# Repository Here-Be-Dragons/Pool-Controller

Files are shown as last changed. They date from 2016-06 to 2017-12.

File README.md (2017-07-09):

# Automated Pool Controller
###### Timer Control of a Hayward Tristar VS Pump and Hayward GL-235 Solar Pool Controller
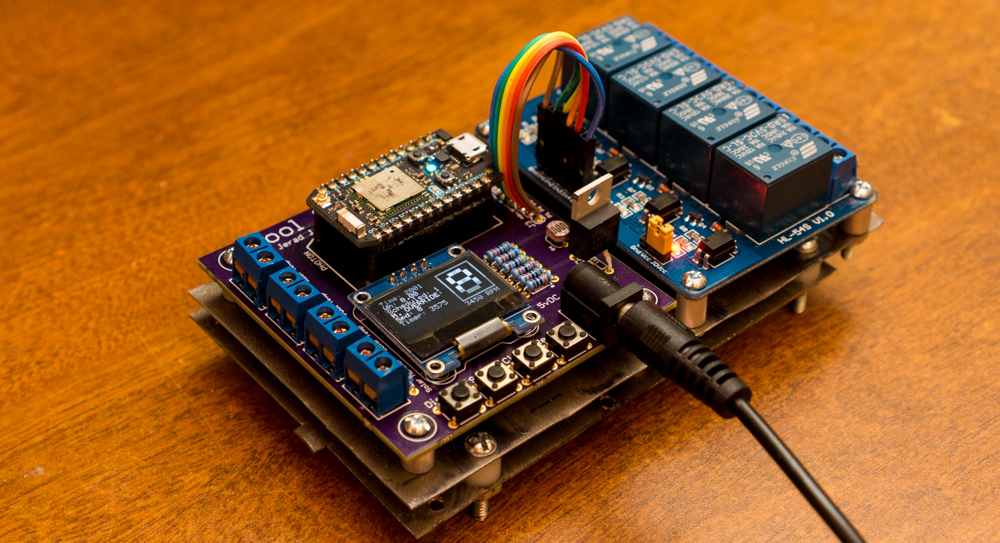
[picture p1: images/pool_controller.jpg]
Finished Pool Controller
  
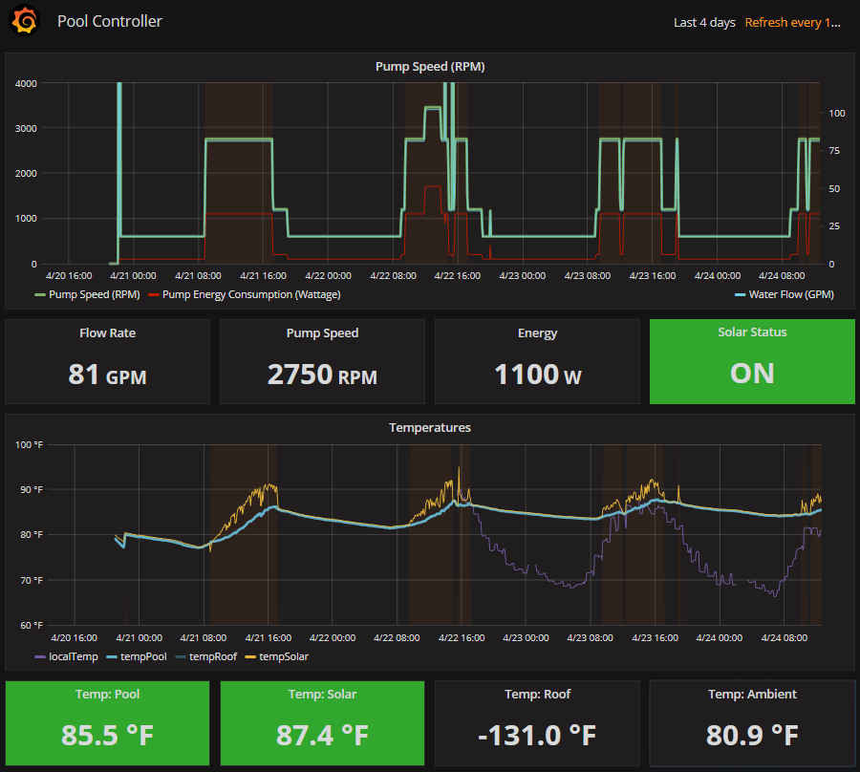
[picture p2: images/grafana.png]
Grafana Dashboard

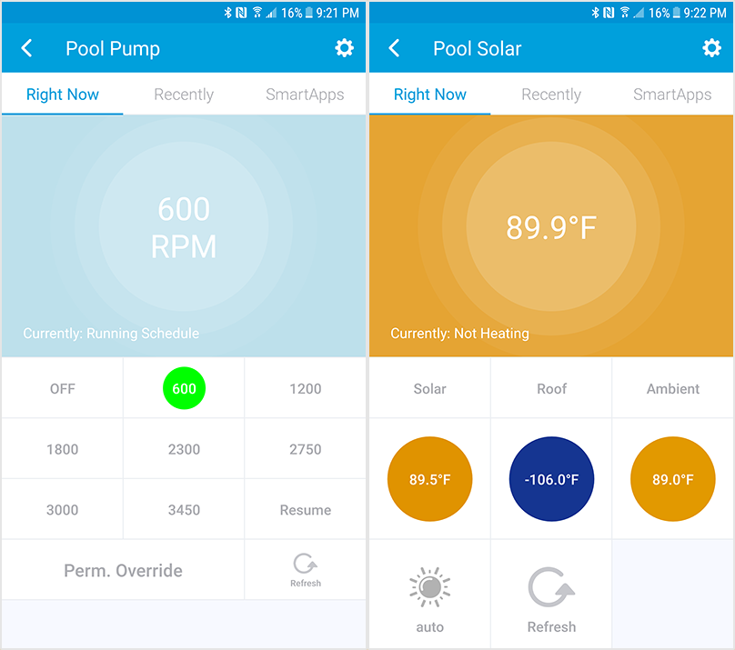
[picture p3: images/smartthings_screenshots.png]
SmartThings Integration

### Overview
---------------------
**Background:**
Due to the engineering principle known as the Pump Affinity Law (<https://en.wikipedia.org/wiki/Affinity_laws>), a very significant energy savings can be had by reducing the speed at which you run your pool pump (approaching 90% savings in an optimal configuration vs. a single-speed pump).  The ideal configuration for energy savings would be to run a pump 24-hours a day at the lowest setting possible to still achieve desired water pumping volume (rule of thumb: 1 pool's water turnover per day), with needed speed-ups at various points during your day to enable the skimmer/vacuum/etc to function.  

My solar heat controller, the Hayward GL-235, actuates a valve to enable or disable the solar panels based on the delta of water temp vs. roof temp, and a maximum temperature setting on the controller itself.  Additionally, according to Hayward, minimum flow for optimal water heating once prime is achieved is 5GPM per panel.  I have 9 panels, so an optimal flow through the solar collectors is 45GPM.  

I do not have a Vacuum system, or other systems that require specific or minimum speed settings.

**The Problem:**
You never know when solar heating will be available.  One day the controller could be calling for heat from 10am to 5pm, and the next it could never reach the delta needed to activate.  Therefore, we need a way to alert the pump to run at the minimum specified speed.

**The Solution:**
An arduino-based butt device called the Particle Photon, with a break-out relay board to activate each of the 3 relays to control speed.  

Code requirements:
-   Easily modified timing
-   Interruptible via buttons+display at controller and/or via phone app (SmartThings)
-   Automatic schedule recovery after a power outage
-   Automatic speed for Solar heater
-   Tracking of a number of values related to the pool:
    -   Water temperature before solar heating
    -   Water temperature after solar heating
    -   Roof temperature
    -   Total kWh used per day
    -   Total gallons pumped per day

The Hayward Tristar VS pool pump has a "third party controls" function that allows you to request a speed based on a combination of 3 relays.  Additionally, the Hayward GL-235 has a relay intended to to trigger a booster pump.  Using both of these facts:  

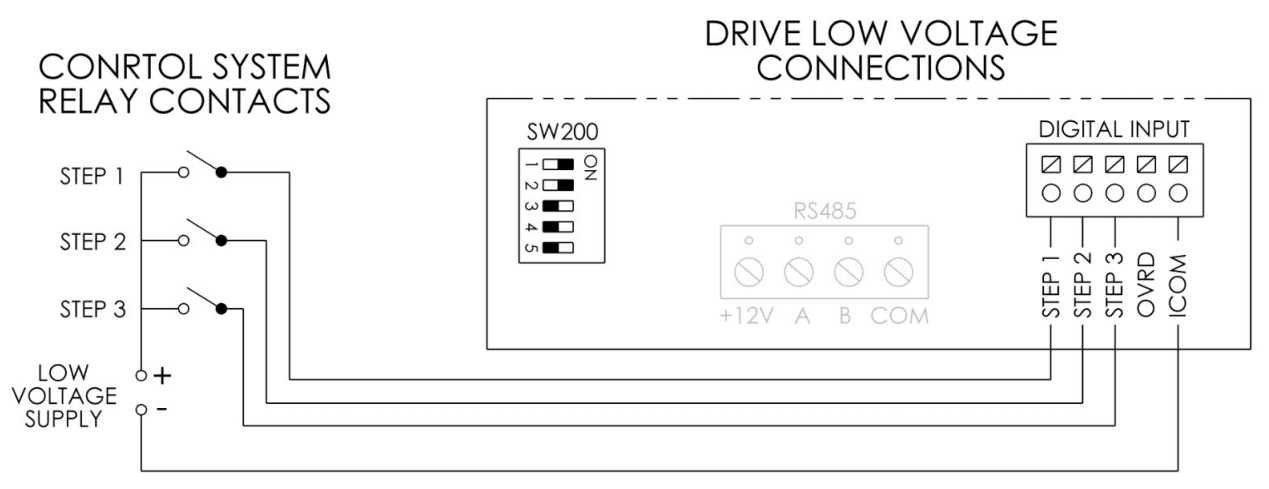
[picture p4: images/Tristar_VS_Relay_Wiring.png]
Pool Pump Diagram


| Timer Speed | STEP 1 Status | STEP 2 Status | STEP 3 Status |
| --- | --- | --- | --- |
| 1 | OFF | OFF | OFF |
| 2 | ON | OFF | OFF |
| 3 | OFF | ON | OFF |
| 4 | ON | ON | OFF |
| 5 | OFF | OFF | ON |
| 6 | ON | OFF | ON |
| 7 | OFF | ON | ON |
| 8 | ON | ON | ON |

The STEP inputs have very wide allowed voltages per the User Manual:
> Inputs are rated to accept a low voltage supply of 18-30VAC (24VAC+/-20%) or 9-30VDC (12/24VDC +/-20%).

Hayward recommends taking power from +12V output to pump controller on RS485 connection as relay source power. "ICOM" (ground) would be jumpered to COM on RS485, so 4-wire connection to the Particle Photon would be:
1.  +12VDC (RS485) &lt;= (White wire) =&gt; Relay inputs
2.  STEP 1 (Relay) &lt;= (Blue wire) =&gt; Relay output
3.  STEP 2 (Relay) &lt;= (Brown wire) =&gt; Relay output
4.  STEP 3 (Relay) &lt;= (Black wire) =&gt; Relay output
    With a 5th internal jumper:
5.  RS485 COM &lt;= =&gt; Digital Input ICOM

(My 4/c wire is white/blue/brown/black)  

From the Photon, I have a wire that runs through the Solar Controller's booster pump relay (I do not have a booster pump) back to an INPUT pin with pulldown circuitry.  This allows the Photon to know when the solar collectors are active and react accordingly.  

Lastly, I have a number of variables made available for my Grafana dashboard with metrics gathered by Collectd:
-   Speed
-   Wattage
-   Flow
-   Solar activity
-   Temperature of pool
-   Temperature after solar
-   Temperature of roof

The first 3 of these are reliant on correct tables in the top of the Photon's code.

### Parts:
-------------------
-   5v-controlled relay with 4 separate relay ports (something like SainSmart 4-Channel Relay Module, <http://www.amazon.com/SainSmart-101-70-101-4-Channel-Relay-Module/dp/B0057OC5O8>)
-   Particle Photon
-   22AWG 4/C 300v wire (Connected to Pump)
-   22AWG 2/C 300v wire (Connected to Solar Controller)
-   0.96" 128x64 SPI/I<sup>2</sup>C OLED Display Module for Arduino (aliexpress.com)
-   Custom printed PCB from Osh Park: https://oshpark.com/shared_projects/181LS60Z
-   10k photoresistor
-   4 2-pin headers
-   4 push buttons
-   Barrel jack connector
-   Various resistors (identified in eagle/Pool_Controller.sch)

### Configuration of code:
-------------------------------------
**speedRPM\[8\]:** Make necessary configurations via the pump controls for speeds you chose, then update the code's array with the pump's speeds.  This ensures proper display values on the OLED, and to any web interfaces/dashboards.

**energyConsum\[8\]:** This is variable based on your installation (head pressure, pipe diameter, etc).  Trigger each configured speed and allow it to stabilize, then record the pump display’s wattage indication to the code's array.

**flowCalc\[8\]:** If you have a flow meter, great, use that.  If not, an estimation can be made using mas985's spreadsheet calculator from the Trouble Free Pools forum.  You can get the latest copy from the below URL.  You want "Pool Pump Tools".
<http://www.troublefreepool.com/threads/830-Hydraulics-101-Have-you-lost-your-head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>

### Other Notes:
-------------------------
**GL-235 Specifics:**  
Do not use the relay on the right side, instead use the one designed for starting a booster pump.  The one on the right side injects 20VAC into the line.

**Data Tracking:**
I have data tracked/graphed using the following:
-   Grafana + InfluxDB + Collectd:
    -   Collectd uses the `curl_json` plugin to query the `pumpSpeed`, `pumpWattage`, `waterFlow`, `solarAct`, and `override` variables
    -   Collectd uses the `network` plugin to output the results to an InfluxDB TSD
    -   Grafana displays the results on a dashboard.
    -   This requires a Linux device running somewhere.  It does not need to have any ports accessible to the internet since it is pulling the data.
    -   See collectd/pool-controller.conf and grafana/pool-controller.json for relevant configuration examples.
-   Google Documents: Particle.Publish() -> IFTTT Recipe -> Google Drive
    -   Recipe example:
        -   If (Event Name): `24Hr_kWh`
        -   is (Event Contents): <Leave Blank>
        -   Device Name or ID: Particle Device being used
        -   Add row to spreadsheet
    -   This is done to track daily power usage and daily gallons pumped.

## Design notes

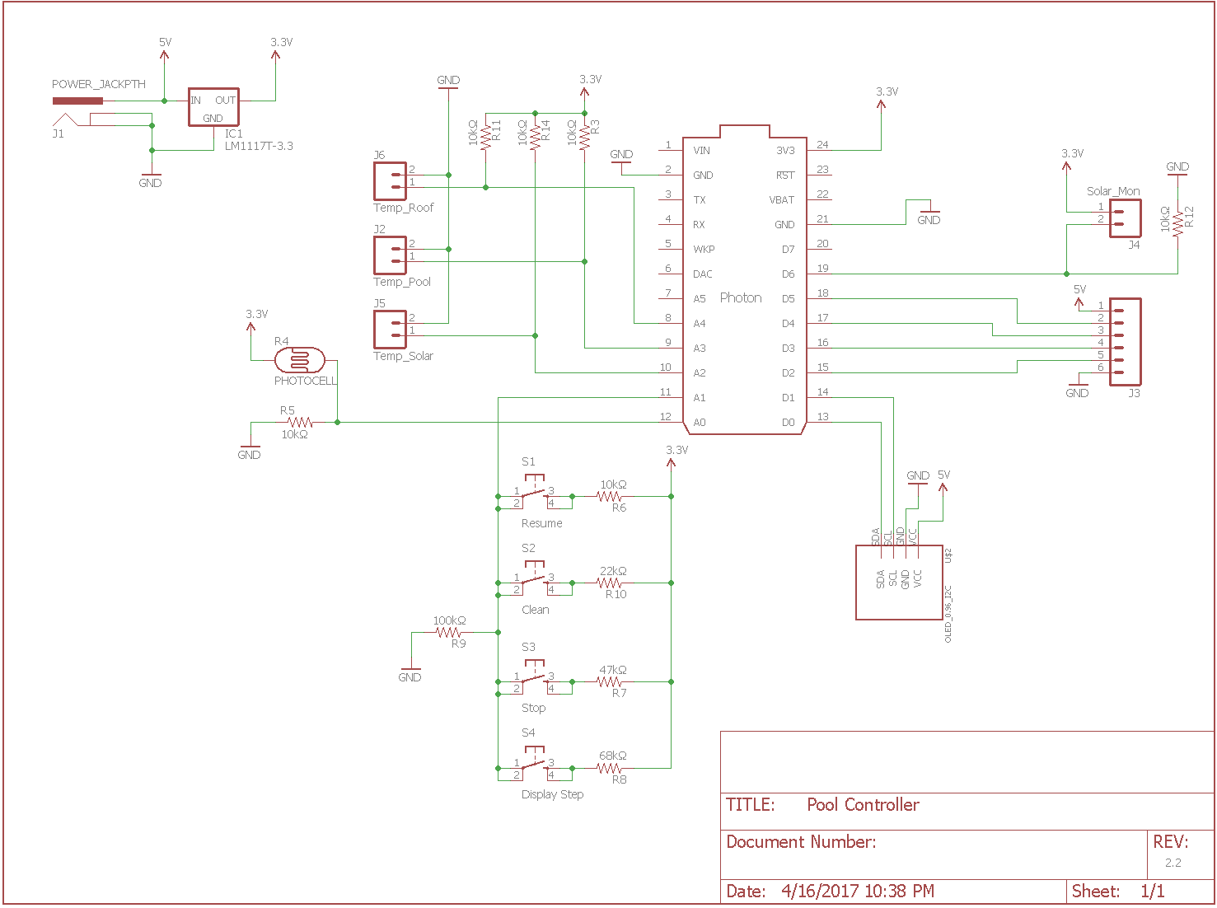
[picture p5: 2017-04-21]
eagle/schematic.png

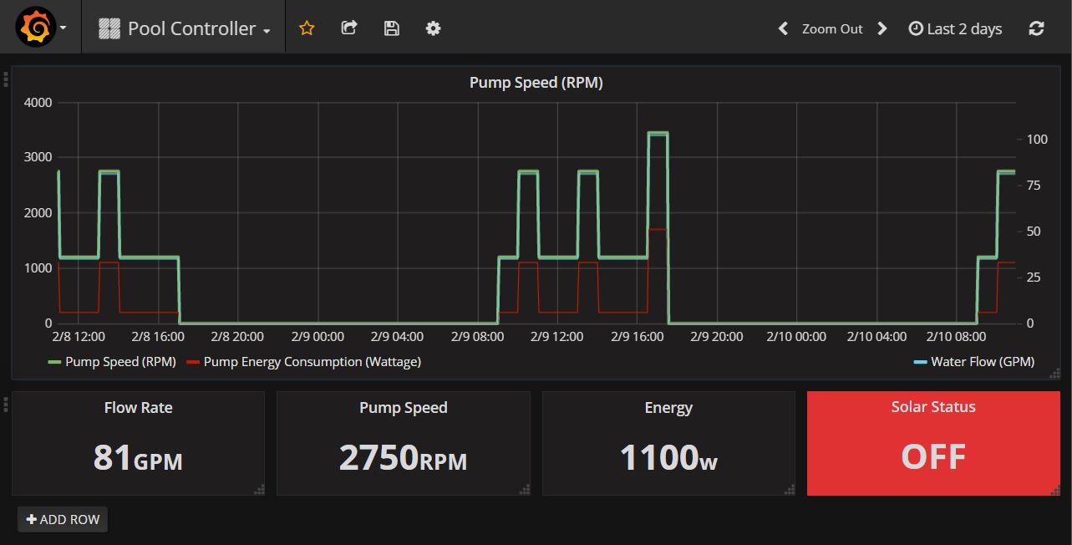
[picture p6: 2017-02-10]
images/grafana.jpg

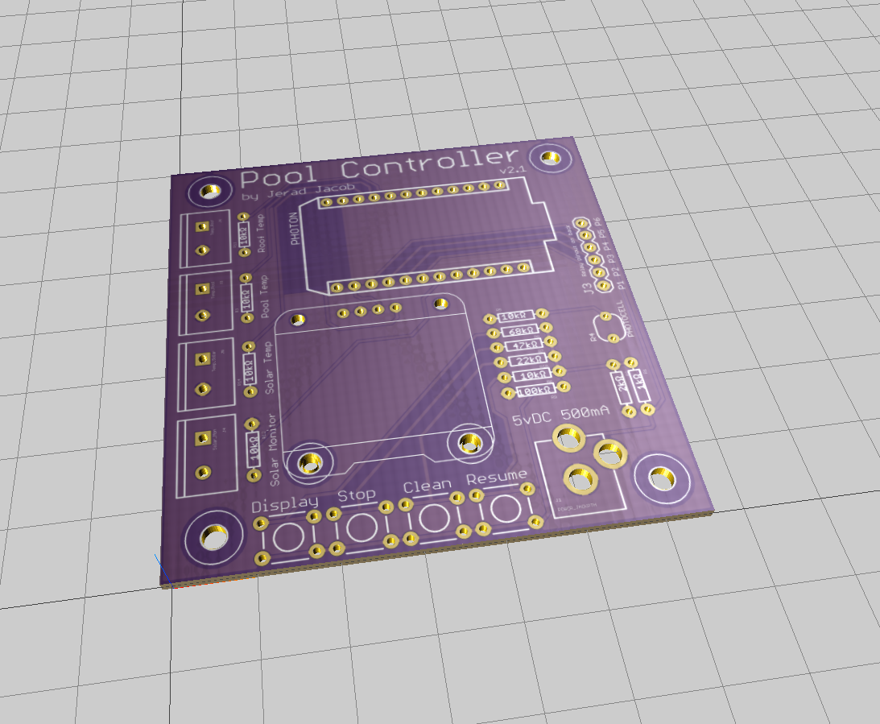
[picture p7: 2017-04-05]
oshpark/3d.png

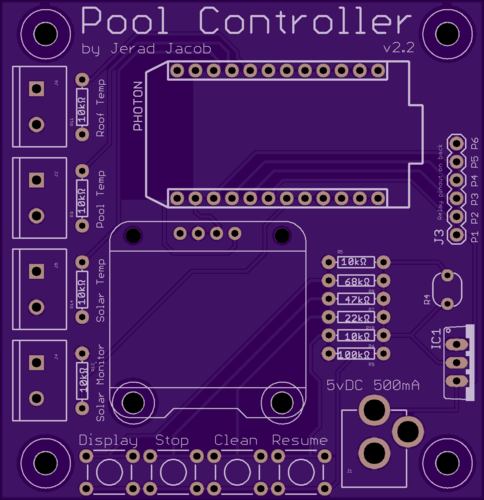
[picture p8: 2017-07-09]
oshpark/front.png

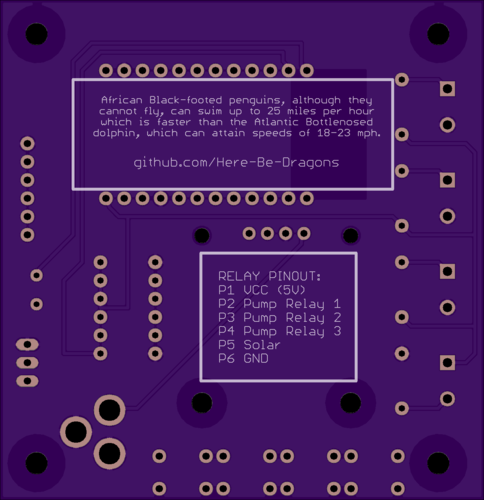
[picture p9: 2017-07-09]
oshpark/back.png

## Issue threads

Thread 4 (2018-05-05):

pump control over rs485

farcouet, 2018-05-05:
Hello,
This is not an issue but just a suggestion: why not controlling the pump via rs485? you can set the rpm as a percentage and the pump will reply with the watt usage. This is the way I control my Hayward pump with a PI.
Cheers,
Fred

Here-Be-Dragons, 2018-05-05:
Do you have more details on this? Obviously I'd prefer to use a comm bus vs. a one-way binary relay mechanism but at the time the protocol was not very well reverse engineered and beyond my capabilities.

farcouet, 2018-05-05:
Sure. Initially I decoded the chlorinator protocol and them when I changed the pump I looked to find if someone already decoded the pump protocol (has I had sold my Hayward OnCommand before I got the pump).

I took the original information from this website: http://www.desert-home.com/2014/07/controlling-hayward-ecostar-pump.html as he decoded some of the pump protocol. I had some issue with the pump watt reply so I did some decoding to find the proper watt information. So there might be some differences depeding of the pump. As soon as you get the pump running it's just a matter of capturing the reply, changing the speed, taking note of what is on the display and comparing to see how is the reply is formatted. The data sent to the pump is the same format and must be sent every second at 19200 bauds. I got first a USB to RS485 adaptor and then replaced it by uart to RS485 converter exactly this one : https://www.ebay.com/itm/Stable-UART-Serial-Port-to-RS485-Converter-Function-Module-RS485-to-TTL-Module/201370097521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

This is the code I wrote (starting with an example of the rexcontrols code as this is what I am using to control the rest of the pool). In the comments you will see some information that I copied from the deserthome webstite to build the code so more details on the website.

/*******************************************************
*                                                      *
*   REXLANG example - data exchange via serial line    *
*                                                      *
*   Sender station                                     *
*                                                      *
*   (c) REX Controls, www.rexcontrols.com              *
*                                                      *
*******************************************************/

// 2017-04-30

#define COM_DEVICE_FNAME 63   // serial device is defined by the fname parameter of the REXLANG block (e.g. /dev/ttyS0 in Linux or COM1: in Windows)

#define COM_BAUDRATE 19200 //baudrate, e.g. 9600, 19200, 57600, 115200

#define COM_PARITY_NONE 0  //no parity
#define COM_PARITY_ODD  1  //odd parity
#define COM_PARITY_EVEN 2  //even parity

#define BUFFER_SIZE  50    //maximum number of bytes to send

//assigning inputs to variables, these variables are READ-ONLY
long input(0) signal0;     //vitesse 1
long input(1) signal1;     //vitesse 2
long input(2) signal2;     //vitesse 3
long input(3) signal3;     //vitesse 4
long output(0) signal4;    //percentage
long output(1) signal5;    //Error flag
long output(2) signal6;    //watts
long output(3) signal7;    //watts

//assigning variables to outputs, these variables are WRITE-ONLY
long output(15) handle;    //handle of the serial device

//declaration of variables
long hCom;                 //communication handle
long buffer[BUFFER_SIZE];  //buffer for incoming data
long dataCnt;              //number of bytes sent
long convData[2];          //array for data conversions

/*
Off  0x10, 0x02, 0x0C, 0x01, 0x00, 0x00, 0x00, 0x1F, 0x10, 0x03

100% 0x10, 0x02, 0x0C, 0x01, 0x00, 0x64, 0x00, 0x83, 0x10, 0x03

45%  0x10, 0x02, 0x0C, 0x01, 0x00, 0x2D, 0x00, 0x4C, 0x10, 0x03

*/
/* Initialization of the REXLANG algorithm */
// the init procedure is executed once when the REXLANG function block initializes
long init(void)
{
  hCom = -1;
	return 0;
}

/* The body of the REXLANG algorithm */
// the main procedure is executed once in each sampling period
long main(void)
{
  if (hCom<0)
  {
    hCom = Open(COM_DEVICE_FNAME,"/dev/ttyUSB1",COM_BAUDRATE,COM_PARITY_NONE);  //opening serial device
  }
  else
  {
	buffer[0] = 0x10;
	buffer[1] = 0x02;
	buffer[2] = 0x0C;
	buffer[3] = 0x01;
	buffer[3] = 0x00;

    if (signal1 == 1)
	{
			buffer[4] = 0x63; // 100%

	}
    else{
		buffer[4] = 0x00;
	}
    buffer[6] =  0x00;
	buffer[7] =  buffer[0] + buffer[1] + buffer[2] + buffer[3] + buffer[4]; // 0x78; // Checksum sum of bytes %256
	buffer[8] = 0x10;
	buffer[9] = 0x03;

    //now all the data can be sent
    dataCnt = Send(hCom,buffer,8); //send data, number of bytes = 21
	buffer[4]=0x00;
	buffer[5]=0xff;

	/*
	It starts off with the begin packet bytes of 0x01, 0x02.  Then 0x00 , 0x0c which would mean, from device 12 to device 0.  Strange that it would reply to device zero when device 1 sent the command, but ??  Byte 6 of the packet is the speed, in the packet above it is byte 6 counting from the first byte being index [0].  Bytes 7 & 8 are the power and they threw me for a loop. They’re in nibble form of the actual speed if you read it out loud. For example:

0x10 0x02 0x00 0x0C 0x00 0x00 0x62 0x17 0x81 0x01 0x18 0x10 0x03

Byte 6 is 0x62, for 98 percent and bytes 7 & 8 are 0x17 0x81, this reads as one, seven, eight, one or a power reading of 1,781 watts. Is that weird or what?   I tried big endian, little endian, hex, some obscure rotations I’ve seen in the past and other stuff until I just happened to read it out loud and then look at the motor. Shocked is probably the correct term for my reaction.
*/

	dataCnt = Recv(hCom,buffer,BUFFER_SIZE); //receive data, max number of bytes = BUFFER_SIZE
	signal4=buffer[7];
	signal6=buffer[8];
	signal7=buffer[9];
  }
  //publishing the serial communication handle through output signal (for debugging)
  handle = hCom;
  return 0;
}

/* Closing the REXLANG algorithm */
//the exit procedure is executed once when the task is correctly terminated
// (system shutdown, downloading new control algorithm, etc.)
long exit(void)
{
	if(hCom>=0) Close(hCom);
  return 0;
}

Mrdindon, 2018-10-31:
Would you be able to helpme with that ?
I'm not able to receive any proper signal from the pump.. I only see a bunch of 0x00 every seconds from the pump when I set the baud rate at 19200... What I tried was to attach the setup as follow :

Pump RS485 port----Rs485to-TTL (thats a module called SH-U12)--------USB-to-TTL (module name CP2102)-----PC running Termite Com5/19200/8N1

I also get the exact same results if I skip the RS485-to-TTL as follow :

Pump RS485 port----USB-to-TTL (module name CP2102)-----PC running Termite Com5/19200/8N1

So I'm receiving something, I can see the RX led flashing every seconds on the usb-to-TTL but it's just not what is expected..

If I lower the baud rate, (to 1200) I see a repeating signal but nothing as described on Desert-Home web site :
01 01 00 00 6b 0d 0a 01 40 00 00 00 00 00 00 00  ....k...@.......
10 00 00 00 00 00 71 0d 0a                       ......q..
01 01 00 00 6b 0d 0a 01 40 00 00 00 00 00 00 00  ....k...@.......
10 00 00 00 00 00 71 0d 0a                       ......q..
01 01 00 00 6b 0d 0a 01 40 00 00 00 00 00 00 00  ....k...@.......
10 00 00 00 00 00 71 0d 0a                       ......q..
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
OvercastBTC, 2023-01-09:
Haha, yes, confirmed that. I guess I was overthinking it a bit. I can just use a smart switch to send the 120 Vac to the doorbell xfmr – for full open/close; I was considering/wanting to have full control of the valve.
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

MYeager1967, 2023-04-30:
I'm in process of refining and adding features to my RPi pool controller. I already have it communicating with HA and opening and closing valves (24v valve actuators using a relay hat) and have been trying to decide whether or not to just wire the motor speeds to a couple of relays or to go the RS485 route. The relays would be easier, but what's the fun in that, right? I have looked at it several times over the past few years and never found much on it other than Dave's work at Desert Home. May have to revisit this again as soon as I get the current projects caught up...

avbdr, 2023-04-30:
> >
>
> Is this in addition to the prime cycle (3 min on my pump)?

Wow. I havent seen this reply. Yes sir, that was it. You have to start the pump at a full 3500RPM for the priming and then you can set any speed you want.

avbdr, 2023-04-30:
@MYeager1967 After 1 year of usage, it seems that my rs485 usage consists of just switching pump to 3500/1500 speeds .
If you just want to have fun -- you can do rs485, if not - you wont lose much with  relay controls (except that you need some more free relays.  If you have hayward pump and this code in this repo  wont work, you can try mine or reuse the code in https://github.com/avbdr/poold/ to see if it will make difference.

MYeager1967, 2023-05-01:
Realistically, I only use 4 of the speeds now and I have 6 relays to work
with. I have plans for some of them, but I only need 2 relays. The RS485
option would give me the possibility of getting data back and possibly even
getting info from my chlorine generator.

On Sun, Apr 30, 2023, 11:45 AM Alexander Butenko ***@***.***>
wrote:

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

avbdr, 2023-05-01:
rs485 is indeed a better way to do it. And a very stable one.

camaro4life18, 2023-05-01:
So I found out there is another protocol the pumps use, which you can't just sniff from the controller on the pump. Its actually a protocol already implemented in nodejs-PoolController found at the link below. I've implemented their whole controller, and its working pretty good. I've found a few issues, but the team that supports it does an excellent job at responding, troubleshooting, and resolving issues.
https://github.com/tagyoureit/nodejs-poolController

rosenhauer, 2024-10-05:
I've delved into decoding the 1200bps motor control code.  I have the following that I can grab from the traffic between the motor and the display.

Called Speed
Actual Speed
Temperature (Repeated 3 times in two different responses) not sure which is which as they all have always matched.
Volts DC
Watts
Amps
Runtime

The numbers have been verified against the onscreen values (some are in the diagnostic menu).

All follow the pattern of: <0x01> <Record Type>, <DATA>, <Checksum> <0x0D> <0x0A>
There are several record types: (Second character of string)
0x01 SET RPM
    RPM is encoded in the  ((CHAR[3] & 0x0F) * 256) + CHAR[2]
0x07 REQUEST INFO
    Request Type is in CHAR[2]  Have only Seen 0x40, 0x55, 0x70
    Immediately after sending the requested record is sent back
0x40 - SPEED INFO
    TempC      = CHAR[10]*256 + CHAR[9]
    ActualRPM  = CHAR[14]*256 + CHAR[13]
0x55 - Unknown only saw it a few times
0x60 - POWER INFO
    VoltsDC       =  CHAR[3]*256 + CHAR[2]
    Amps           = (CHAR[5]*256 + CHAR[4])/10
    Wattage        = CHAR[7]*256 + CHAR[6]
    TempA        = CHAR[9]*256 + CHAR[8]
    TempB        = CHAR[11]*256 + CHAR[10]
    Runtime   = CHAR[14]*256 + CHAR[13]*256 + CHAR[12])/10  Time is in munutes and displayed in the controller screen as xx.x hours.

The numbers have been verified against the onscreen values (some are in the diagnostic menu).

But I still can't figure out the checksum.  I thought I had it and was able to decode some of them but an offset keeps changing and I haven't been able to figure it out completely.  So I may have to punt back to just sending the known codes to the motor and not actually generate the checksums but use the known ones from the scans.

After reading through this and other blogs it looks like if I change the DIP switch on the motor that it will change the protocol to the "standard" 19200baud format that the universal controllers use. I haven't tried that yet but if that is the case then I may drop the included controller and just replicate all of the functionality in my EPS32 controller that I have for the rest of the pool stuff.  If that isn't the case then I will continue to try and decode the checksum.

Dave

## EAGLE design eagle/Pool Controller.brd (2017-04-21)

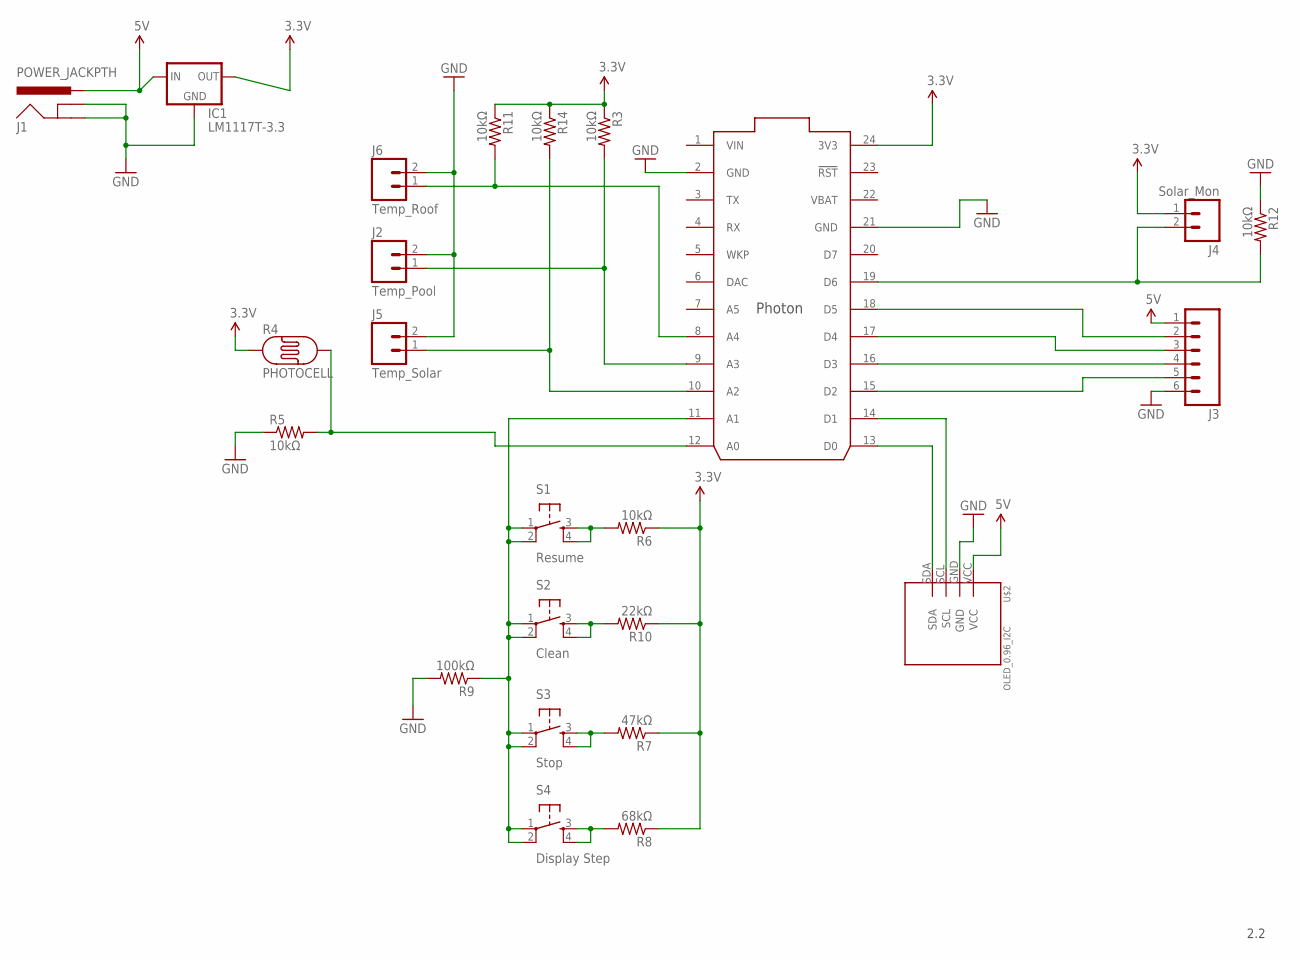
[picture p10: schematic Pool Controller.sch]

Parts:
IC1: LM1117T-3.3; TO220V
J1: POWER_JACKPTH; POWER_JACK_PTH
J2: Temp_Pool; SCREWTERMINAL-5MM-2
J3: M06SILK_FEMALE_PTH; 1X06
J4: Solar_Mon; SCREWTERMINAL-5MM-2
J5: Temp_Solar; SCREWTERMINAL-5MM-2
J6: Temp_Roof; SCREWTERMINAL-5MM-2
PHOTON: PHOTON_WITH_HEADERS; PHOTON
R3, R5, R6, R11, R12, R14: 10kΩ; AXIAL-0.3
R4: PHOTOCELL
R7: 47kΩ; AXIAL-0.3
R8: 68kΩ; AXIAL-0.3
R9: 100kΩ; AXIAL-0.3
R10: 22kΩ; AXIAL-0.3
S1: Resume; TACTILE-PTH
S2: Clean; TACTILE-PTH
S3: Stop; TACTILE-PTH
S4: Display Step; TACTILE-PTH
U$2: OLED_0.96_I2C

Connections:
3.3V: IC1.2 (OUT), J4.1, PHOTON.24 (3V3), R3.P$1 (1), R4.1, R6.P$1 (1), R7.P$1 (1), R8.P$1 (1), R10.P$1 (1), R11.P$1 (1), R14.P$1 (1)
5V: IC1.3 (IN), J1.PWR, J3.1, U$2.VCC
GND: IC1.1 (GND), J1.GND, J1.GNDBREAK, J2.2, J3.6, J5.2, J6.2, PHOTON.2 (GND), PHOTON.21 (GND), R5.P$1 (1), R9.P$2 (2), R12.P$1 (1), U$2.GND
unnamed: J3.5, PHOTON.15 (D2)
unnamed: J3.4, PHOTON.16 (D3)
unnamed: PHOTON.13 (D0), U$2.SDA
unnamed: PHOTON.14 (D1), U$2.SCL
unnamed: PHOTON.12 (A0), R4.2, R5.P$2 (2)
unnamed: J3.3, PHOTON.17 (D4)
unnamed: J3.2, PHOTON.18 (D5)
unnamed: R7.P$2 (2), S3.3, S3.4
unnamed: J4.2, PHOTON.19 (D6), R12.P$2 (2)
unnamed: R10.P$2 (2), S2.3, S2.4
unnamed: J5.1, PHOTON.10 (A2), R14.P$2 (2)
unnamed: J2.1, PHOTON.9 (A3), R3.P$2 (2)
unnamed: R8.P$2 (2), S4.3, S4.4
unnamed: PHOTON.11 (A1), R9.P$1 (1), S1.1, S1.2, S2.1, S2.2, S3.1, S3.2, S4.1, S4.2
unnamed: R6.P$2 (2), S1.3, S1.4
unnamed: J6.1, PHOTON.8 (A4), R11.P$2 (2)
VBAT: PHOTON.22 (VBAT)
VIN: PHOTON.1 (VIN)

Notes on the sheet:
2.2

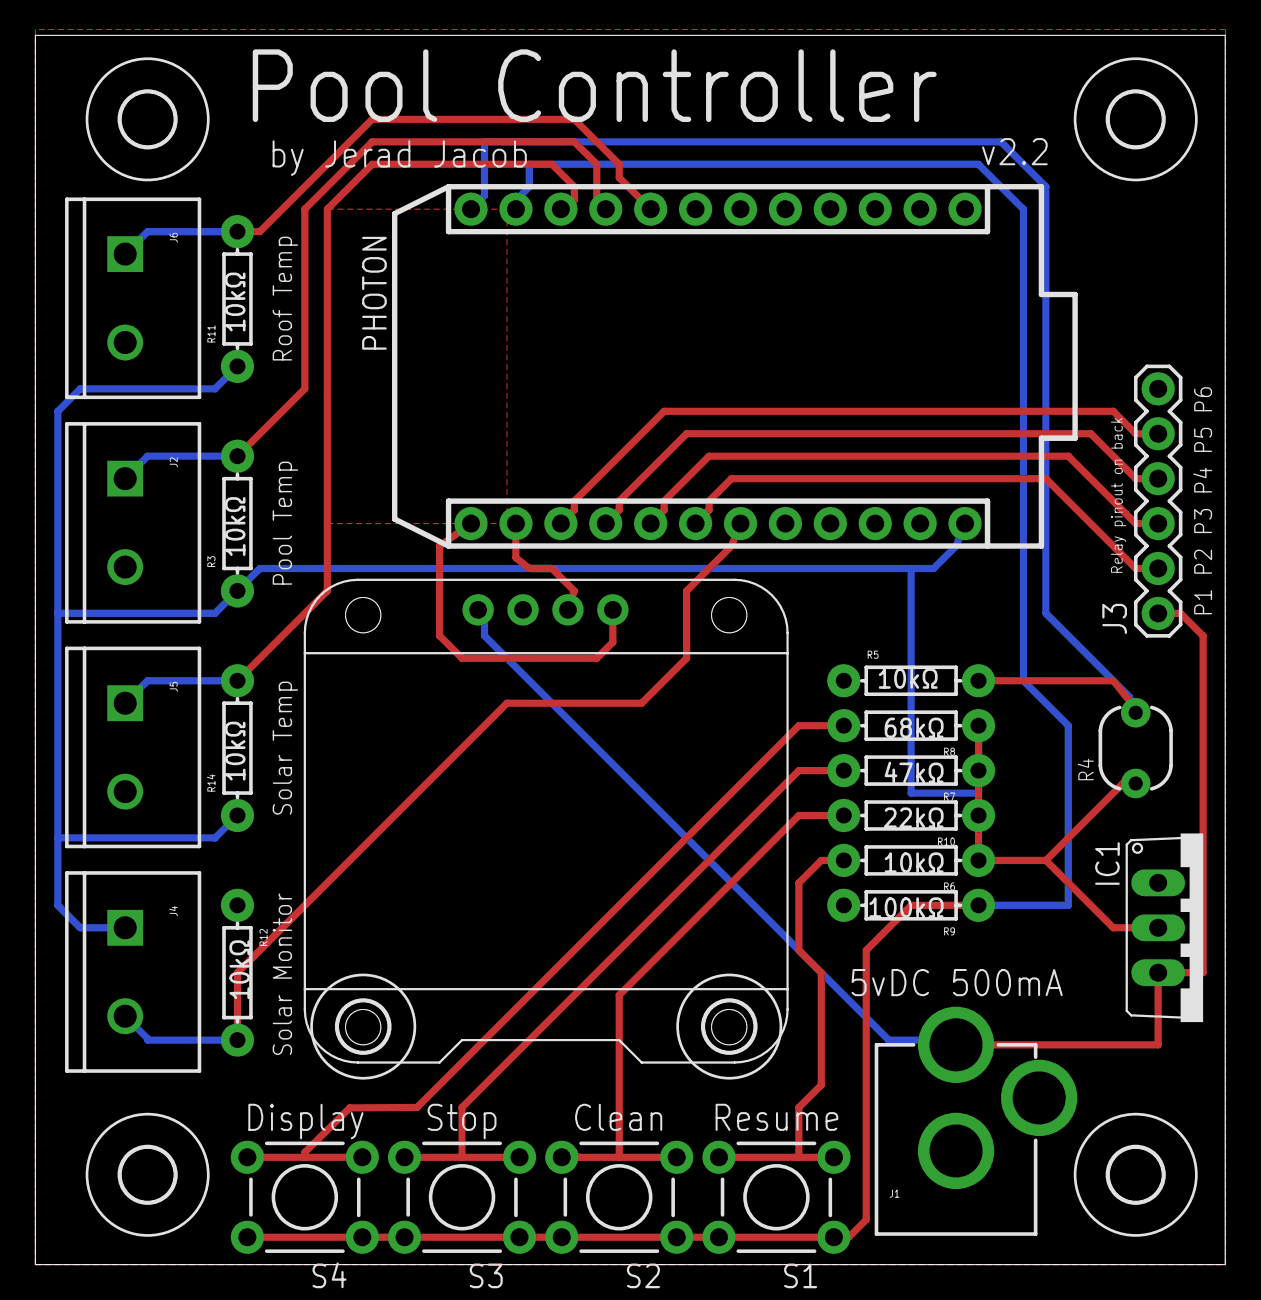
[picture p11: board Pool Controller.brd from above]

Board: 2 copper layers, 67.3 x 69.5 mm, 30 parts (0 on the bottom side), 19 nets.

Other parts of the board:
U$1, U$7: 2,8
U$3, U$4, U$5, U$6: 3,0

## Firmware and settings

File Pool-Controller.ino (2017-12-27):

// Automated Pool Controller
// v2.3
// by Jerad Jacob
// Refer to README.md for additional information and latest updates
// https://github.com/Here-Be-Dragons/Pool-Controller

// This #include statement was automatically added by the Particle IDE.
#include <photon-thermistor.h>

// This #include statement was automatically added by the Particle IDE.
#include <Adafruit_SSD1306.h> //OLED

SYSTEM_MODE(SEMI_AUTOMATIC); //Prevent blocking on setup()
SYSTEM_THREAD(ENABLED); //Prevents blocking code when offline.

////
//Start of user configurations
////

// Update the below array with the settings from 
// the pump for output to the Screen, SmartThings, and
// estimating turnover/energy use.  This doesn't actually
// change the speeds on the pump, it's just bookkeeping.
// speedRPM[0] must be 0 to turn the pump off
// 1200RPM is the minimum speed for chlorinator flow sensor
// 2750RPM is the recommended speed for 9 solar panels (~45GPM)
// 3450RPM for pool cleaning
uint16_t speedRPM[8] = {0,600,1200,1800,2300,2750,3000,3450};

// Manually trigger each of the above speeds and record their
// energy usage (Watts) below for accurate consumption tracking
uint16_t energyConsum[8] = {5,100,200,400,800,1100,1400,1700};

// Estimate total gallons of flow per minute for each speed
uint16_t flowCalc[8] = {0,18,35,53,68,81,88,102};

// Default length (in seconds) to run manual Overrides
// Applied if no time is specified in override
uint16_t defaultOverride = 3600;

// Time Zone offset
int16_t timeZone = -5;

// Calibration for light sensor.
// 30 is a reasonable value if the box is tightly sealed.
uint16_t dispMinBrightness = 100;

// Set the speed the pump will run for manual pool cleaning
uint8_t cleanSpeed = 8;

// Set the minimum speed the pump will run when solar is active
uint8_t minSolarSpeed = 6; 

// Speed activation times in HHMM format. If two speeds have the same
// time entered, the higher speed takes precidence.  Leave off any
// preceeding zeros, as they will prevent a proper match.


/////
//Winter Schedule
/////
uint16_t aSpeed1[] = {0,                  1700}; //    0 RPM
uint16_t aSpeed2[] = {                        }; //  600 RPM
uint16_t aSpeed3[] = { 900,   1100,   1400    }; // 1200 RPM
uint16_t aSpeed4[] = {                        }; // 1800 RPM
uint16_t aSpeed5[] = {                        }; // 2300 RPM
uint16_t aSpeed6[] = {    1000,   1300        }; // 2750 RPM
uint16_t aSpeed7[] = {                        }; // 3000 RPM
uint16_t aSpeed8[] = {                        }; // 3450 RPM

/*
/////
//Summer Schedule
/////
uint16_t aSpeed1[] = {0,                  1900}; //    0 RPM
uint16_t aSpeed2[] = {                        }; //  600 RPM
uint16_t aSpeed3[] = { 900,   1100,   1400    }; // 1200 RPM
uint16_t aSpeed4[] = {                        }; // 1800 RPM
uint16_t aSpeed5[] = {                        }; // 2300 RPM
uint16_t aSpeed6[] = {    1000,   1300        }; // 2750 RPM
uint16_t aSpeed7[] = {                        }; // 3000 RPM
uint16_t aSpeed8[] = {                        }; // 3450 RPM
*/
// Button resistances (found via manual probing, see test-buttons.ino)
// Only needs to be within +/- 15 of actual measured value to account for noise
uint16_t buttonResist1 = 2435;
uint16_t buttonResist2 = 2790;
uint16_t buttonResist3 = 3360;
uint16_t buttonResist4 = 3725;

// Voltage divider resistor values for thermistors.  These need to be reasonably exact
uint16_t rPool = 10090;
uint16_t rSolar = 10040;
uint16_t rRoof = 10030;

////
//End of user configurations
////

// This value persists permanently on the Photon even after flashes/reboots
STARTUP(WiFi.selectAntenna(ANT_EXTERNAL)); // Use external antenna
//STARTUP(WiFi.selectAntenna(ANT_INTERNAL)); // Use internal antenna

time_t currentEpochTime = 0;    //The current Epoch time set at the beginning of each loop in getTimes()
uint16_t currentTime = 0;       //Friendly time converted from currentEpochTime via convertTime(), 10:00 PM is referenced as 2200
uint16_t previousTime = 0;      //The time as of the last loop, set at the bottom of loop()
char publishString[40];         //Temporary string to use for Particle.publish of WhTally
uint16_t currentSpeed = 0;      //The current motor speed setting number (1-8)
uint16_t overrideSpeed;         //Stores the override speed when set manually
//uint16_t lastChange;          //Time the speed was last changed via scheduler (not currently used)
uint16_t scheduledSpeed = 0;    //What speed the schedule says you should be at
uint8_t manualOverride = 0;     //0 for scheduled, 1 for override with schedule, 2 for indefinite override.  Changes via user intervention
time_t overrideStarted;         //This is set to currentEpochTime when a manual override is triggered
time_t overrideEnds = 0;        //This is set to currentEpochTime + overrideLength when a manual override is triggered
uint32_t overrideLength = 0;    //Recieved override length in seconds.

uint8_t lastDay;                //Used for onceADay()
uint8_t lastMinute;             //Used for onceAMinute()

//Variables for Photoresistor
bool isBright = 1;              //Tracks whether the screen should be lit or not.

//Variables for buttons
long lastDebounceTime = 0;      // the last time the output pin was toggled
long debounceDelay = 25;        // Adjust for jitter (if you get a false reading increase this number)
uint8_t buttonState = 0;        // the current reading from the input pin
uint8_t lastButtonState = 0;    // the previous reading from the input pin
uint8_t lastActionedButton = 0; // the last button actioned

//Variables for Temperature Sensors
float poolTempF;
float solarTempF;
float roofTempF;
float ambTempF;

//Variables for Solar Heating
uint8_t solarControl = 2;      // Manual control of solar. 0 = override to off, 1 = override to on, 2 = Solar Controller
bool autoOverride = 1;          // Changes when solar kicks on. 0 = scheduled speed, 1 = solar min. speed override
bool solarRequest;              // Request from Hayward controller

//Variables for reporting
time_t previousDataPublish;     //Webhook publish tracking (Epoch)
double WhTally = 0;             //Daily count of Wh consumption, to upload to Google Docs for tracking
double gallonTally = 0;         //Daily count of Gallons pumped, to upload to Google Docs for tracking
String sSpeed;
String sWattage;
String sFlow;
String sSolar;
String sOverride;
String sTempSolar;
String sTempPool;
String sTempRoof;
String sTempAmb;
String sButton;
String sResist;
String sIllum;
String sOverrideEnds;
String sValuesST;
String sSolarST;

//Variables for Display
uint8_t displayIndex = 0;
time_t oledOverrideUntil = 0;
uint8_t oledOverrideIndex = 0;
uint8_t oledOverrideTimer = 0;

// Assign pins to relays
// D0 reserved for SDA of OLED
// D1 reserved for SCL of OLED
#define pPumpRelay1     D2
#define pPumpRelay2     D3
#define pPumpRelay3     D4
#define pRelay4         D5
#define pSolarRelay1    D6
#define OLED_RESET      WKP //Not sure what this is for, not connected
#define pLED            D7 
#define pButtons        A1
#define pIllum          A0
#define pTempSolar      A2
#define pTempPool       A3
#define pTempRoof       A4

Adafruit_SSD1306 oled(OLED_RESET);

// For an NTC (negative temperature coefficient) thermistor only!
// CONSTRUCTOR PARAMETERS:
// 1. pin: Photon pin
// 2. seriesResistor: The resistance value of the fixed resistor (based on your hardware setup)
// 3. adcMax: The maximum analog-to-digital convert value returned by analogRead (Photon is 4095 NOT the typical Arduino 1023!)
// 4. thermistorNominal: Resistance at nominal temperature (will be documented with the thermistor, usually "10k")
// 5. temperatureNominal: Temperature for nominal resistance in celcius (will be supplied with the thermistor, assume 25 if not stated)
// 6. bCoef: Beta coefficient of the thermistor; usually 3435 or 3950 (will be documented with the thermistor)
// 7. samples: Number of analog samples to average (for smoothing)
// 8. sampleDelay: Milliseconds between analog samples (for smoothing)
Thermistor solarTherm = Thermistor(pTempSolar, rSolar, 4095, 10800, 25, 3950, 3, 5); //5 8
Thermistor poolTherm  = Thermistor(pTempPool,  rPool,  4095, 10900, 25, 3850, 3, 5);
Thermistor roofTherm  = Thermistor(pTempRoof,  rRoof,  4095, 10000, 25, 3921, 3, 5);

void setup() {
    
    pinMode(pPumpRelay1,    OUTPUT); // Pump Relay 1
    pinMode(pPumpRelay2,    OUTPUT); // Pump Relay 2
    pinMode(pPumpRelay3,    OUTPUT); // Pump Relay 3
    pinMode(pRelay4,        OUTPUT); // Solar Actuator Relay
    //pinMode(pSolarRelay1,   INPUT); // Solar panel on pulls this up to 3.3v.
    pinMode(pLED, OUTPUT);//DEBUG

    oled.begin(SSD1306_SWITCHCAPVCC, 0x3C);    // Initialize with the I2C addr 0x3D (for the 128x64 screen)
    Particle.function("mOverride", mOverride); // Listen for a manual override via remote user input for pump
    Particle.function("solarCmd", solarCmd); // Listen for a manual override via remote user input for solar
    Particle.variable("pumpSpeed", sSpeed);
    Particle.variable("pumpWattage", sWattage);
    Particle.variable("waterFlow", sFlow);
    Particle.variable("solarAct", sSolar);
    Particle.variable("override", sOverride);
    Particle.variable("tempSolar", sTempSolar);
    Particle.variable("tempPool", sTempPool);
    Particle.variable("tempRoof", sTempRoof);
    Particle.variable("valuesST", sValuesST); // Values to export to SmartThings Device Type
    Particle.variable("solarST", sSolarST); // Values to export to SmartThings Device Type
    
    // I have a weather station that is already sending Webhooks to DarkSky.net.
    // This just listens for the response and parses out local ambient air temp.
    // The weather station project is here: 
    Particle.subscribe("290023001047343339383037/hook-response/weather/", gotWeatherData, MY_DEVICES);
    
    Particle.connect(); // Needed in SEMI_AUTOMATIC
   
    for (int x = 10; x > 0; x--){                   // Give it x seconds to stabilize the RTC and get a time from NTP
        oled.clearDisplay();                       // Clear Screen
        oled.drawRect(0,0,128,64, WHITE);
        oled.drawRect(1,1,127,63, WHITE);
        oled.setTextColor(WHITE);
        oled.setCursor(5,5);
        oled.setTextSize(1);
        oled.println("Pool-Controller v2.2");
        oled.print("    by Jerad Jacob");
        oled.setCursor(30,50);
        oled.print("Startup: ");
        oled.print(x);
        oled.display();
        delay(1000);
    }
    
    Time.setDSTOffset(1);
    Time.zone(timeZone);
    
    onceADay();
    getTimes();         // Set up initial times
    returnToSchedule(); // Find what the current speed should be
}

void loop() {
    catchButtonPresses();
    updateDisplay();
    
    // True once every day
    if (lastDay != Time.day()) {
        onceADay();
    }
    if (lastMinute != Time.minute()) {
        onceAMinute();
    }
    checkIllum();
    getTimes();

    //Check for expired manual Override
    if( manualOverride == 1 ) {
        if (overrideEnds <= currentEpochTime) {
            returnToSchedule();
        }
    }
    
    //Activate new speed if there is one
    setPumpSpeed();
    
    //Check solar state and set transformer
    setSolar();
}

//Finds the current time each loop
void getTimes(){
    //Gets Time-zone adjusted Epoch Time from the cloud, and converted HHMM comparison time
    currentEpochTime = Time.now();
    currentTime = convertTime(currentEpochTime);
}

void onceADay(){
    //Manual DST logic
    if( Time.month() < 3 || (Time.month() == 3 && Time.day() <=13) || (Time.month() == 11 && Time.day() >=6) || Time.month() > 11 ){
        Time.endDST();
    }else{
        Time.beginDST();
    }
    lastDay = Time.day();
}

void onceAMinute(){
    //Check for new scheduled speed
    scheduledSpeed = findScheduledSpeed(currentTime);
    getTemps();
    WhTally += (double) ( energyConsum[currentSpeed-1] / 60 ); // Add 1 minute worth of kWh
    gallonTally += (double) ( flowCalc[currentSpeed-1] );      // Add 1 minute worth of water flow
    trackData();
    lastMinute = Time.minute();
}

uint16_t convertTime(uint32_t testTime){
    //Converts Epoch to HHMM
    uint16_t returnTime;
    returnTime = Time.hour(testTime) * 100 + Time.minute(testTime);
    return returnTime;
}

uint16_t findScheduledSpeed(uint16_t atTime){ // Find the Scheduled Speed
    uint16_t x = scheduledSpeed;
    for (uint16_t i=0; i < sizeof(aSpeed1) / sizeof(uint16_t); i++) {
        if ( aSpeed1[i] == atTime ) {
            x = 1;
        }
    }
    for (uint16_t i=0; i < sizeof(aSpeed2) / sizeof(uint16_t); i++) {
        if ( aSpeed2[i] == atTime ) {
            x = 2;
        }
    }
    for (uint16_t i=0; i < sizeof(aSpeed3) / sizeof(uint16_t); i++) {
        if ( aSpeed3[i] == atTime ) {
            x = 3;
        }
    }
    for (uint16_t i=0; i < sizeof(aSpeed4) / sizeof(uint16_t); i++) {
        if ( aSpeed4[i] == atTime ) {
            x = 4;
        }
    }
    for (uint16_t i=0; i < sizeof(aSpeed5) / sizeof(uint16_t); i++) {
        if ( aSpeed5[i] == atTime ) {
            x = 5;
        }
    }
    for (uint16_t i=0; i < sizeof(aSpeed6) / sizeof(uint16_t); i++) {
        if ( aSpeed6[i] == atTime ) {
            x = 6;
        }
    }
    for (uint16_t i=0; i < sizeof(aSpeed7) / sizeof(uint16_t); i++) {
        if ( aSpeed7[i] == atTime ) {
            x = 7;
        }
    }
    for (uint16_t i=0; i < sizeof(aSpeed8) / sizeof(uint16_t); i++) {
        if ( aSpeed1[8] == atTime ) {
            x = 8;
        }
    }
    return x;
}

void setPumpSpeed() {
    uint8_t newSpeed;
    newSpeed = scheduledSpeed;
  
    //Set Manual Override Speed to newSpeed if active
    if( manualOverride != 0 ){
        newSpeed = overrideSpeed;
    }
  
    //If auto override is active, set a minimum speed
    if( autoOverride == 1 && newSpeed < minSolarSpeed ){
        newSpeed = minSolarSpeed;
    }
    switch (newSpeed) {
        case 1:
            digitalWrite(pPumpRelay1, LOW );
            digitalWrite(pPumpRelay2, LOW );
            digitalWrite(pPumpRelay3, LOW );
            break;
        case 2:
            digitalWrite(pPumpRelay1, HIGH);
            digitalWrite(pPumpRelay2, LOW );
            digitalWrite(pPumpRelay3, LOW );
            break;
        case 3:
            digitalWrite(pPumpRelay1, LOW );
            digitalWrite(pPumpRelay2, HIGH);
            digitalWrite(pPumpRelay3, LOW );
            break;
        case 4:
            digitalWrite(pPumpRelay1, HIGH);
            digitalWrite(pPumpRelay2, HIGH);
            digitalWrite(pPumpRelay3, LOW );
            break;
        case 5:
            digitalWrite(pPumpRelay1, LOW );
            digitalWrite(pPumpRelay2, LOW );
            digitalWrite(pPumpRelay3, HIGH);
            break;
        case 6:
            digitalWrite(pPumpRelay1, HIGH);
            digitalWrite(pPumpRelay2, LOW );
            digitalWrite(pPumpRelay3, HIGH);
            break;
        case 7:
            digitalWrite(pPumpRelay1, LOW );
            digitalWrite(pPumpRelay2, HIGH);
            digitalWrite(pPumpRelay3, HIGH);
            break;
        case 8:
            digitalWrite(pPumpRelay1, HIGH);
            digitalWrite(pPumpRelay2, HIGH);
            digitalWrite(pPumpRelay3, HIGH);
            break;
        //This condition should never happen, but default to Speed 1 if it does
        default:
            digitalWrite(pPumpRelay1, LOW );
            digitalWrite(pPumpRelay2, LOW );
            digitalWrite(pPumpRelay3, LOW );
            returnToSchedule(); //Try a schedule reset
            break;
    }
    currentSpeed = newSpeed; //Update current speed value
}

void setSolar() {
    //Check Solar Controller for request to heat.  Applies in setPumpSpeed()
    solarRequest = digitalRead(pSolarRelay1);
    
    if (solarControl == 0) { // Manual Override: Disable Solar
        digitalWrite(pRelay4, LOW);
        autoOverride = 0;
    } else if (solarControl == 1) { // Manual Override: Enable Solar
        digitalWrite(pRelay4, HIGH);
        autoOverride = 1;
    } else { // System follows ext. controller
        if (solarRequest == 1){
            digitalWrite(pRelay4, HIGH);
            autoOverride = 1;
        } else {
            digitalWrite(pRelay4, LOW);
            autoOverride = 0;
        }
    }
}

int mOverride(String command) { //Manual Trigger (SmartThings, button press, etc)
    char strBuffer[63] = ""; //Max length of the Function String is 63 characters
    command.toCharArray(strBuffer, 63);
    overrideSpeed = atoi(strtok(strBuffer, "~"));
    overrideLength = atoi(strtok(NULL, "~"));
    manualOverride = atoi(strtok(NULL, "~"));
    if (overrideSpeed == 0 && manualOverride == 1) { //Add the specified time to existing override
        Particle.publish("Pool Debug", "adding 60 minutes to override");
        overrideEnds = overrideEnds + overrideLength;
    }
    if (overrideSpeed <= 8 && overrideSpeed >= 1){ //These are direct speeds
        if (manualOverride == 1) {
            overrideStarted = currentEpochTime;
            if (overrideLength == 0 ){ //Use default override length
                overrideEnds = currentEpochTime + defaultOverride;
            }else{
                overrideEnds = currentEpochTime + overrideLength;
            }
        }
        setPumpSpeed();
    }
    if( manualOverride == 0 ){ //0 is a "return to schedule"
        returnToSchedule();
    }
    // DEBUG
    String sSpeedRecieved = String(overrideSpeed);
    String sTimeRecieved = String(overrideLength);
    String sOverride = String(manualOverride);
    Particle.publish("Speed_Recieved", sSpeedRecieved + ", " + sTimeRecieved + ", " + sOverride);
    // END DEBUG
    overrideLength = 0; //Reset overrideLength
    trackData();
    return speedRPM[currentSpeed-1];
}

int solarCmd(String command) { //Manual Trigger for Solar
    solarControl = atoi(command);
    setSolar();
    trackData();
    return poolTempF;
}

void returnToSchedule() {
    scheduledSpeed = 0;
    uint32_t testTimeEpoch = currentEpochTime;
    uint16_t testTime;
    while( scheduledSpeed == 0 ) {
        testTime = convertTime(testTimeEpoch);
        scheduledSpeed = findScheduledSpeed(testTime);
        testTimeEpoch-=60;
    }
    manualOverride = 0;
    overrideSpeed = 0;
    overrideStarted = 0;
    delay(2000);
}

// Prevent OLED burn-in by turning off the screen when
// the door is shut.
void checkIllum(){
    uint16_t currentIllum = analogRead(pIllum);
    if (currentIllum > dispMinBrightness) {
        isBright = 1;
    } else {
        isBright = 0;
    }
    sIllum = String(currentIllum);
}

void getTemps(){
    if (currentSpeed != 1) {
        solarTempF = solarTherm.readTempF();
        poolTempF = poolTherm.readTempF();
    }
    roofTempF = roofTherm.readTempF();
    
    sTempSolar = String(solarTempF);
	sTempPool = String(poolTempF);
	sTempRoof = String(roofTempF);
}
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

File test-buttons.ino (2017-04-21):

#define buttonPin       A1   // the number of the pushbutton pin
#define ledPin          D7   // the number of the LED pin for testing.  D7 is integrated into the photon.

// Array for each button consists of {low,high} values that should
// count as a button press.  If you don't know the values yet, press each
// button and monitor the output of the "resistance" Particle variable
const uint16_t aButton1[2] = {2420,2450};
const uint16_t aButton2[2] = {2780,2810};
const uint16_t aButton3[2] = {3340,3370};
const uint16_t aButton4[2] = {3710,3740};
 

uint8_t buttonState = 0;     // the current reading from the input pin
uint8_t lastButtonState = 0; // the previous reading from the input pin

// the following variables are long's because the time, measured in miliseconds,
// will quickly become a bigger number than can be stored in an int.
long lastDebounceTime = 0;   // the last time the output pin was toggled
int debounceDelay = 50;     // the debounce time; increase if the output flickers

String sResistance;
String sButton;

void setup() {
    pinMode(ledPin, OUTPUT);
    Particle.variable("resistance",sResistance);
    Particle.variable("buttonpr",sButton);
}

void loop() {
    // read the state of the switch into a local variable:
    uint16_t reading = analogRead(buttonPin);
    sResistance = String(reading);
    uint8_t tmpButtonState = 0;
    
    if(reading > aButton4[0] && reading < aButton4[1]){
        tmpButtonState = 4;
    }else if(reading > aButton3[0] && reading < aButton3[1]){
        tmpButtonState = 3;
    }else if(reading > aButton2[0] && reading < aButton2[1]){
        tmpButtonState = 2;
    }else if(reading > aButton1[0] && reading < aButton1[1]){
        tmpButtonState = 1;
    }else{
        tmpButtonState = 0; //No button is pressed;
    }
    
    // check to see if you just pressed the button 
    // (i.e. the input went from LOW to a buttonState), and you've waited 
    // long enough since the last press to ignore any noise:  
    
    // If the switch changed (due to noise OR pressing)
    if (tmpButtonState != lastButtonState) {
        // reset the debouncing timer
        lastDebounceTime = millis();
    }

    if ((millis() - lastDebounceTime) > debounceDelay) {
        // Assume this state is legitimate, so set it as buttonState
        buttonState = tmpButtonState;
        switch(buttonState){
            case 1:
                digitalWrite(ledPin, HIGH);
                sButton = String("BUTTON 1: Display");
                break;
            case 2:
                digitalWrite(ledPin, HIGH);
                sButton = String("BUTTON 2: Stop");
                break;
            case 3:
                digitalWrite(ledPin, HIGH);
                sButton = String("BUTTON 3: Clean");
                break;
            case 4:
                digitalWrite(ledPin, HIGH);
                sButton = String("BUTTON 4: Resume");
                break;
            default:
                digitalWrite(ledPin, LOW);
                sButton = String("---");
                break;
        }
    }
    
    lastButtonState = tmpButtonState;
}

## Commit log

2016-05-14 Partially Complete Device Type
2016-05-20 Fixed compile-time errors. IT COMPILES!!!
    [Pool-Controller.ino]
2016-05-20 Fixed oled linebreaks
    logic still janky
    [Pool-Controller.ino]
2016-05-30 Implemented DST, fixed some Epoch conversion bugs
    [Pool-Controller.ino]
2016-06-05 First working version
    -Keeps a schedule
    -Allows Manual Override
    -Overrides correctly for auto override
    -Hunts for the correct time in the event of an interruption
    [Pool-Controller.ino]
2016-06-06 Added additional instrumentation to ThingSpeak
    -Speed
    -Wattage
    -Flow
    -Solar On/Off
2016-07-05 Fixed indenting
    maybe spaces will be next
    [Pool-Controller.ino]
2016-07-05 Updated schedule to never turn pump off
    6am priming of pump was waking me up
2016-08-10 Fixed OLED to use new overrideEnds function
    [Pool-Controller.ino]
2016-08-10 Added external antenna call
2017-02-10 Initial working version of Device Handler
2017-02-10 Major rework
    NEW FEATURES:
    - Now works with SmartThings! Still needs some cleanup to the Device Handler at a later date.
    - Updated README.md with additional screenshot and files for Dashboarding
    BUG FIXES:
    - SmartThings speed selection now works.
2017-03-30 Initial Schematic Design
    [Pool Controller.sch]
2017-03-31 Updated Eagle Files
    [Pool Controller.brd, Pool Controller.sch]
2017-03-31 Finished initial design
    [Pool Controller.brd, Pool Controller.sch]
2017-03-31 Updated Eagle files for PCB v2.1
    [Pool Controller.brd, Pool Controller.sch]
2017-04-01 Added photo sensor tracking
2017-04-03 Added 3 Thermistors and Screen on/off sensor
    Added function from here: http://playground.arduino.cc/ComponentLib/Thermistor2?action=sourceblock&num=3
    We'll see if it works.
2017-04-11 Added 3.3v Regulator
    [Pool Controller.brd, Pool Controller.sch]
2017-04-11 Revert "Added 3.3v Regulator"
    This reverts commit 23a2b24274d4a83250f4b2e9a9d27c3bcc80a4d5.
    [Pool Controller.brd, Pool Controller.sch]
2017-04-12 Changed type of tmpButtonState to match buttonState
2017-04-13 corrected relay pinout
    [Pool Controller.brd, Pool Controller.sch]
2017-04-13 Major Code Rework
    FEATURES:
    - Pool temperature tracking
    - Post-solar temperature tracking
    - Roof temperature tracking
    - OLED turn-off when electrical box is closed
    - Physical button interface to display:
    - Display Cycle
    - Change pump speed: stopped
    - Change pump speed: cleaning mode
    - Resume programmed speeds
    - Reworked display GUI
    - Solar on/off override
    [Pool-Controller.ino]
2017-04-13 Moved to Photon-Thermistor library
2017-04-15 Implemented display blanking + bugfixes
    NEW FEATURES
    - Display blanking when dark (door closed)
    BUG FIXES
    - Photoresistor variable value set to uint8_t instead of uint16_t, causing rollover
    [Pool-Controller.ino]
2017-06-26 Updated for new SmartThings Device Handler
    Added significant featureset to Device Handler for SmartThings
2017-07-09 Working SmartThings with Pump + Solar
    - Works with SmartThings Solar Device Type
    BUGFIX:
    - Pump Override Time sent to SmartThings is correct
    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
    [Pool-Controller.ino]
2017-07-09 Removed deprecated DeviceType
    Use `hayward-vs-pool-pump.src` instead
2017-07-09 Fixed 5v to 3v to use Regulator
    [Pool Controller.sch]
2017-07-09 Updated render for v2.2 board revision
2017-07-09 Redirected OSHPark URL
    To v2.2 of board to fix regulator
2017-07-09 Removing old board photo
    Replaced with PCB board
2017-12-27 Stop logging temps when pump is off

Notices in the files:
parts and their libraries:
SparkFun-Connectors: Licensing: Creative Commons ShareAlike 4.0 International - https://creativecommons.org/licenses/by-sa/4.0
